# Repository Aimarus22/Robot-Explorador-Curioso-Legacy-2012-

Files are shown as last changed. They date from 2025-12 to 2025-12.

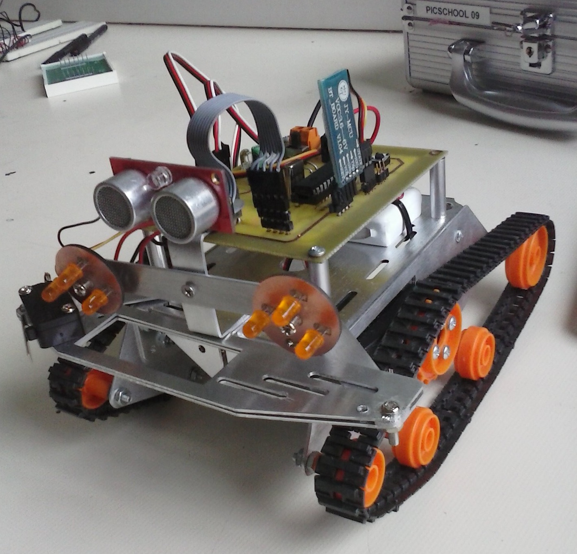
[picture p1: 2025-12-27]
docs/REC.jpg

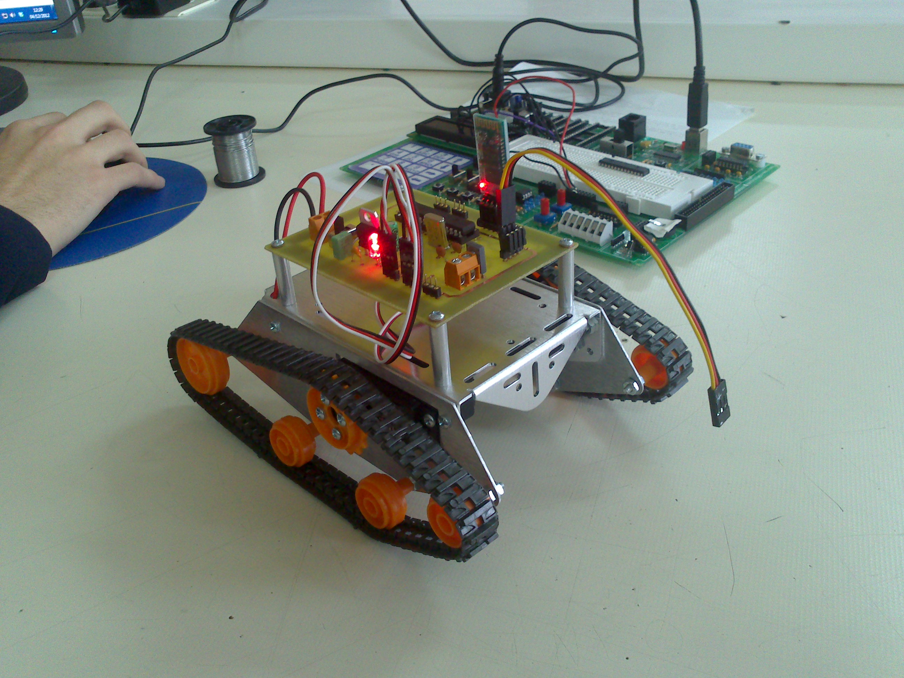
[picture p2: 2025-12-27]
docs/DSC_0086.jpg

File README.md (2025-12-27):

# Robot Explorador Curioso (Legacy 2012) 🤖

> **3er Premio - Premios Don Bosco (DBSariak) 2013**
> *Innovación en Electrónica y Robótica*

Este repositorio sirve como cápsula del tiempo para la preservación digital del proyecto **"Robot Explorador Curioso"**, desarrollado íntegramente en el curso 2012-2013 como proyecto PBL de fin del Ciclo Formativo de Grado Superior en Desarrollo de Productos Electrónicos en **La Salle Berrozpe** (Andoain).

## Objetivos del Repositorio

Este archivo no es solo un backup, tiene un doble propósito académico y de investigación:

1.  **Preservación Histórica:** Mantener accesible el código fuente, esquemas y documentación original tal y como fueron concebidos en 2012-2013, sin refactorizaciones modernas, para documentar el estado del arte de la educación técnica de la época.
2.  **Estudio Comparativo (Arqueología de Software):** Servir como "Línea Base" (v.0) para analizar la evolución de la ingeniería de sistemas embebidos. El objetivo futuro es contrastar estas técnicas "bare-metal" artesanales (control de tiempos por software, gestión manual de registros) con implementaciones modernas (RTOS, periféricos dedicados, TinyML) en la misma plataforma robótica.

## Autores y Créditos
Proyecto desarrollado por el equipo técnico de "Robotic Solutions" (empresa simulada para el proyecto PBL):

* **Axier Albín** - *Desarrollo de aplicación Android.*
* **Jokin Mugika** - *Diseño Mecánico, fabricación de PCB, montaje y puesta a punto.*
* **Aimar Rollán-González** - *Firmware, gerbers y documentación.*

**Institución:** La Salle Berrozpe (Andoain, Gipuzkoa, España).

## Stack Tecnológico (La "Vieja Escuela" de 2012)
El robot destaca por integrar múltiples subsistemas complejos en un microcontrolador de 8 bits con recursos limitados, utilizando técnicas de programación de bajo nivel hoy en desuso en favor de capas de abstracción (HAL).

* **Microcontrolador:** Microchip **PIC16F876A** (8-bit, 20MHz).
* **Lenguaje:** C (Compilador CCS).
* **Hardware:** PCB diseñada a medida en **OrCAD** y fabricada/soldada manualmente.
* **Sensores:** Ultrasonidos SRF08 (protocolo I2C implementado a mano) + Telemetría de batería (Calibración ADC empírica).
* **Actuadores:** Servomotores de rotación continua controlados mediante **PWM por Software (Bit-Banging)**.
* **Comunicación:** Módulo Bluetooth (UART) + App Android nativa (App Inventor).

## Estructura del Repositorio

* `/firmware`: Código fuente original (`main.c`) recuperado del archivo de 2013. Muestra la implementación manual de la máquina de estados y los retardos bloqueantes (`delay_us`) para la generación de señales.
* `/hardware`: Archivos de diseño electrónico (Esquemáticos, PCBs y Gerbers) generados con OrCAD.
* /applet_android : Programa original .apk
* `/docs`: Memoria técnica completa, incluyendo el Plan de Negocio ficticio y diagramas de flujo.

## Nota de Preservación
El código contenido en la carpeta `/firmware` se presenta **"tal cual" (as-is)** fue compilado en enero de 2013. Contiene prácticas de programación específicas de aquel contexto (uso de retardos bloqueantes para temporización, variables globales, números mágicos) que se mantienen deliberadamente para preservar la integridad histórica y permitir el análisis comparativo con versiones futuras optimizadas.

---
*Repositorio mantenido por Aimar Rollán-González como parte del proyecto de investigación sobre evolución de sistemas embebidos (2012-2026).*

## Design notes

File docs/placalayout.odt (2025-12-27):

VISTA GENERAL EN LAYOUT PLUS

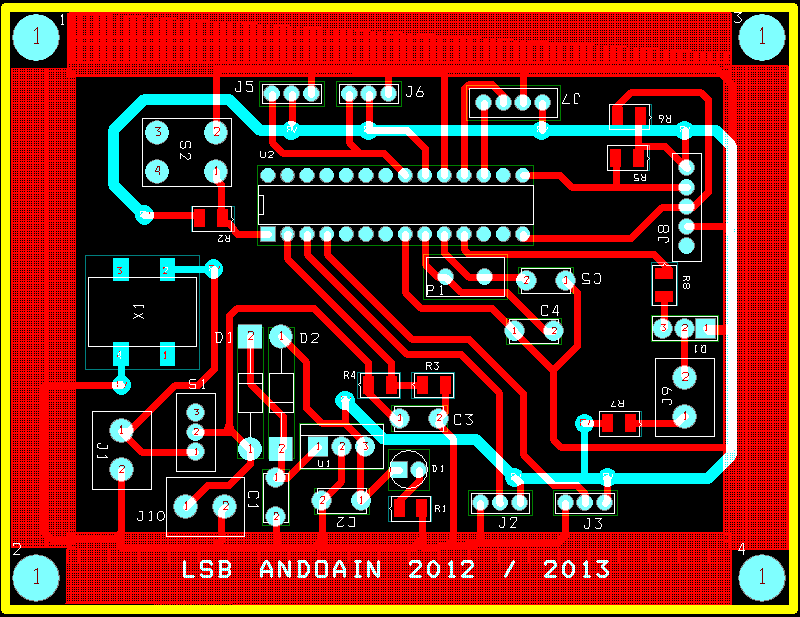
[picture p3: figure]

Instrucciones de montaje:

- Fijarse en la orientación de los componentes.
- El pad cuadrado de algunos componentes corresponde a su pin 1.
- Las resistencias SMD van todas en la cara Bottom.
- Todas las vías son de 1mm.
- Los agujeros de soporte son de 3 mm.
- Broca de 0.8 mm: condensadores, cristal, diodo led, botón reset, regletas y zócalo PIC.
- Broca de 1 mm: diodos, interruptor, LM7805, transistor.
- Broca de 1.2 mm:Regleta naranja (batería, cámara y linterna).

C1: 330nF P1: Cristal

C2: 100nF Q1: Transistor BD139

C3: 1uF (pol.) R1: 220Ω

C4: 22pF R2: 1KΩ

C5: 22 pF R3: 4K7Ω

D1: led verde R4: 4K7Ω

D2: 1N4007 R5: 4K7Ω

D3: 1N4007 R6: 4K7Ω

J1: Regleta batería R7: 15Ω

J2: Regleta motor D R8: 5K4Ω

J3: Regleta motor I S1: Interruptor

J5: Regleta F. C. 1 S2: Pulsador reset

J6: Regleta F. C. 2 U1: LM7805

J7: Regleta bluethoot U2: Zócalo PIC 28 patas

J8: Regleta sonar X1: Cargador de batería SMD

J9: Regleta linterna

J10: Regleta cámara

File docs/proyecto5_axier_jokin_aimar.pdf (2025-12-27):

PROYECTO ROBOT EXPLORADOR

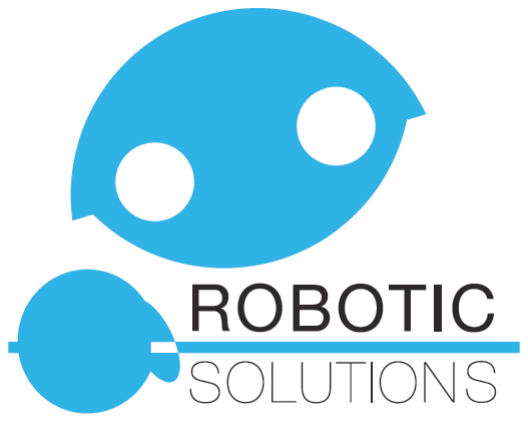
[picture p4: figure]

ÍNDICE

1-. INTRODUCCIÓN | pag. 1
2-. LA IDEA DE NEGOCIO | pag. 2
3-. LOS PROMOTORES | pag. 4
4-. ESTUDIO DE MERCADO | pag. 5
4.1-. ANÁLISIS DEL SECTOR Y LA COMPETENCIA | pag. 6
4.2-. CLIENTES POTENCIALES | pag. 7
4.3-. ANÁLISIS DAFO | pag. 8
5-. EL PLAN DE NEGOCIO | pag. 9
5.1-. EL PLAN DE MARKETING | pag. 9
-. PRODUCTO | pag. 9
-. PRECIO | pag. 11
-. PROMOCIÓN | pag. 12
-. DISTRIBUCIÓN | pag. 15
-. PREVISIÓN DE VENTAS | pag. 15
5.2-. EL PLAN DE INVERSIONES Y COMPRAS | pag. 18
-. INVERSIÓN INICIAL | pag. 18
-.PLANIFICACIÓN DEL PEDIDO | pag. 21
5.3-. EL PLAN DE PRODUCCIÓN | pag. 22
-. UNIDADES A PRODUCIR | pag. 22
-. CÁLCULO DE COSTES Y TIEMPOS | pag. 23
5.4-. EL PLAN DE RECURSOS HUMANOS | pag. 30
-. FORMA JURÍDICA DE LA EMPERSA | pag. 32
5.5-. LOCALIZACIÓN DE LA EMPRESA | pag. 35
5.6-. PLAN ECONÓMICO FINANCIERO | pag. 38
-. PLAN DE FINANCIACIÓN | pag. 38
-. PREVISIONES DE VENTAS | pag. 40
-. BALANCE INICIAL | pag. 41
-. PREVISIÓN DE TESORERÍA | pag. 45
-. CONCLUSIONES SOBRE LA VIABILIDAD | pag. 2

I

6-. MEMORIA TÉCNICA DEL PROYECTO | pag. 47
6.1.- MEMORIA DESCRIPTIVA | pag. 47
6.2.- PLIEGO DE CONDICIONES | pag. 80
6.3.- CÁLCULOS JUSTIFICATIVOS | pag. 83
6.4.- PLANOS Y ESQUEMAS | pag. 90
6.5.- PROGRAMACIÓN DEL PIC | pag. 91
6.6.- CREACIÓN DEL APPLET DE ANDROID | pag. 91
6.7.- CÁLCULO DEL COSTE DEL PROTOTIPO | pag. 94
7-. CONCLUSIÓN | pag. 98
8-. BIBLIOGRAFÍA | pag. 99
ANEXO I: RESULTADOS DE LAS ENCUESTAS DEL ESTUDIO DE MERCADO
ANEXO II: PLANOS DE ORCAD CAPTURE
ANEXO III: PLANOS DE ORCAD LAYOUT
ANEXO IV: PROGRAMA COMPLETO EN LENGUAJE C

ANEXO VI: DATASHEETS DE LOS COMPONENTES DEL CIRCUITO ANEXO VII: MANUAL DE USUARIO

II

## 1-. INTRODUCCIÓN

En el presente informe se expondrán todos los detalles de nuestro proyecto así como la presentación de nuestra empresa ROBOTIC SOLUTIONS. Trataremos de que todo el trabajo de estos últimos meses quede reflejado en él.

## 2-. LA IDEA DE NEGOCIO

Una idea de negocios es una descripción de un posible negocio de éxito. Para que sea buena ha de cumplir ciertos requisitos, tales como:

– | Ha de ser breve, clara y atractiva.
– | Ha de cubrir una demanda no satisfecha en la sociedad, o en caso de que
ya esté cubierta, ofrecer algo mejor o más barato que lo ya existente.
– | Ha de ser rentable económicamente.
– | Su fabricación ha de ser viable para la empresa que la quiera desarrollar.

Nuestra idea de negocio es la de construir un robot explorador de conductos de aire acondicionado y venderlo a buen precio en un nicho de mercado poco explotado, pero también dejando un margen para futuros nuevos productos relacionados con la robótica.

Para desarrollar esta idea y ver si es viable haremos un estudio de mercado, tal como veremos en el apartado 4.

Por otra parte, el nombre de nuestra empresa será: ROBOTIC SOLUTIONS S.coop. (utilizaremos la Cooperativa como forma jurídica de constituir nuestra empresa). Ofreceremos, tal como su nombre indica, soluciones robóticas. Nuestro mercado estará enfocado inicialmente a pequeños robots móviles, destinados a brindar apoyo industrial o doméstico en tareas en las que el ser humano no pueda llegar.

Nuestro logotipo empresarial es el siguiente:

ROBOTIC SOLUTIONS apuesta por la innovación, la creatividad y la calidad de sus productos, así como un precio asequible para llevar sus soluciones robóticas al máximos número de personas.

## 3-. LOS PROMOTORES

Los promotores de este proyecto somos:

– | Axier Albín.
– | Jokin Mujika.
– | Aimar Rollan.

Somos tres técnicos superiores en electrónica, formados en La Salle Berrozpe de Andoain, en la promoción de 2011 – 2013.

## 4-. ESTUDIO DE MERCADO

A través de esta investigación queremos comprobar haber si tenemos un nicho sin explotar en el mercado y en el caso contrario, averiguar si hay un hueco en el mercado para lanzar nuestro producto y saber qué nos diferencia de nuestros posibles competidores en cuanto a las ventajas como a las desventajas.

Para ello necesitaremos saber la aceptación que tendrá nuestro producto en el mercado a que precio estarían dispuestos a comprarlo y por qué comprarían nuestro producto en vez de el de nuestros competidores.

Las fuentes de información serán las siguientes: El mercado objetivo (competencia), posibles clientes, Internet, Instituto nacional de Estadística, Boletín Oficial del Estado (BOE), Registro Mercantil, Registro de la Propiedad, Oficina Española de Patentes y Marcas...

La Técnica de recolección de datos que utilizaremos en gran medida serán las encuestas, ya sean individuales o en grupo, “Focus Grup” y sondeos. Una muestra de nuestra encuesta realizada se adjunta en el Anexo I del presente informe.

4.1.- Análisis del sector y la competencia:

El sector de la robótica en España no está muy masificado, pero las pocas empresas existentes poseen productos adaptados a todas las necesidades de los potenciales clientes. En el País Vasco no existe ninguna empresa que venda robots de inspección de conductos de aire acondicionado, por lo que esa puede ser nuestra principal baza, a pesar de que hoy en día la venta online está en boga y casi todos los competidores tienen una cobertura nacional.

Principales competidores:

– Iberbotics. Santander. Producen y venden el robot explorador de conductos iVision 1.0, un robot de excelente apariencia, robusto, fiable, con 5 años de garantía y una vida útil estimada de unos 15 años.
– Robotnik Automation. Valencia. No poseen robots de inspección de conductos de aire, pero en las categorías de vigilancia, exploración y rescate, sus modelos parecen insuperables. Sus robots son de gran tamaño y de precios astronómicos. Tienen el monopolio de las agencias de protección civil así como las policiales.
– Eventronics. Alicante. Disponen de varios modelos de robots de inspección e incluso limpieza (por medio de escobillas rotativas acoplables e inyección de aire y productos desinfectantes) con bastante buena pinta.
– Trenz-Cleaner. Barcelona. Un único modelo de robot explorador y limpiador de conductos. El robot parece un poco “casero” y su página web no es muy profesional.
– Quark Robotics. Madrid. Su producto estrella es el Cruiserbot, un robot explorador de apariencia muy robusta y compacta, capaz de superar cualquier obstáculo dentro de una tubería.

– Roboserv. Tarragona. Disponen de tres modelos de robot exploradores, con un diseño avanzado y diseñados específicamente para explorar conductos de aire.

Todas estas empresas venden sus robots bajo presupuesto, adaptándolo a las necesidades del cliente, pero ninguno baja de los 3000 euros.

Con estos datos, y teniendo en cuenta que todos venden sus productos a nivel nacional con soporte técnico incluido, nuestra oportunidad de hacernos un hueco en el mercado es ofreciendo un producto considerablemente más barato que el de ellos.

4.2.- Clientes potenciales:

Nuestros clientes potenciales serán principalmente las empresas de instalación, mantenimiento y limpieza de aires acondicionados. En menor medida instituciones gubernamentales y de servicios de seguridad, y algún caso aislado de alguna institución arqueológica. Venderlo como juguete es otra opción, o incluso en centros educativos.

Como uso doméstico no tiene aplicaciones, por lo que nuestra área se reduce al ámbito profesional específico; además cada empresa necesitaría como máximo, y siendo muy optimistas, cinco robots exploradores en caso de empresas grandes con varias inspecciones simultáneas. Además, hay que tener en cuenta que el producto tiene una vida útil bastante larga, de unos cinco años aproximadamente, y que posee un año de garantía; por lo tanto una vez vendido obtendremos poco beneficio del mismo cliente en los primeros años.

En el País Vasco existen una centena de clientes potenciales dedicados al mantenimiento y limpieza de conductos, por lo que es imperativo ampliar el mercado a empresas de seguridad privada, ya que las instituciones gubernamentales, policiales y arqueológicas son tan reducidas en número que una venta sería casi un milagro.

4.3.- Análisis DAFO:

Debilidades:

– | Diseño sencillo.
– | Chasis no demasiado robusto.
– | El producto no es nuevo en el mercado.

Amenazas:

– | Pocos clientes potenciales.
– | Sector muy competitivo.
– | Producto de larga vida (pocas ventas por cliente).

Fortalezas:

– | Precio más bajo que la competencia.
– | Manejo vía smartphone y tablet.

Oportunidades:

– | En el País Vasco no hay empresas que vendan este producto.
– | Podemos venderlo online a otras comunidades o incluso a otros países.

## 5-. EL PLAN DE NEGOCIO

5.1-. PLAN DE MÁRKETING Y VENTAS

Este apartado consiste en establecer una estrategia con el objeto de introducir el producto o servicio en el mercado, alcanzando el volumen de ventas inicialmente previsto. Esta estrategia se funda principalmente en las decisiones sobre el precio, las decisiones de promoción y las decisiones de distribución.

PRODUCTO

Nuestro producto estrella, y único producto de momento, todo hay que decirlo, es el robot explorador “Curioso”, ideado para introducirse por los conductos de ventilación de aires acondicionados y detectar su estado interno. Dónde el ojo humano no ve, el robot
entra en acción, pues
gracias a sus sensores
puede enviar información al usuario. Se dirige desde un dispositivo Android y posee un precio competitivo.

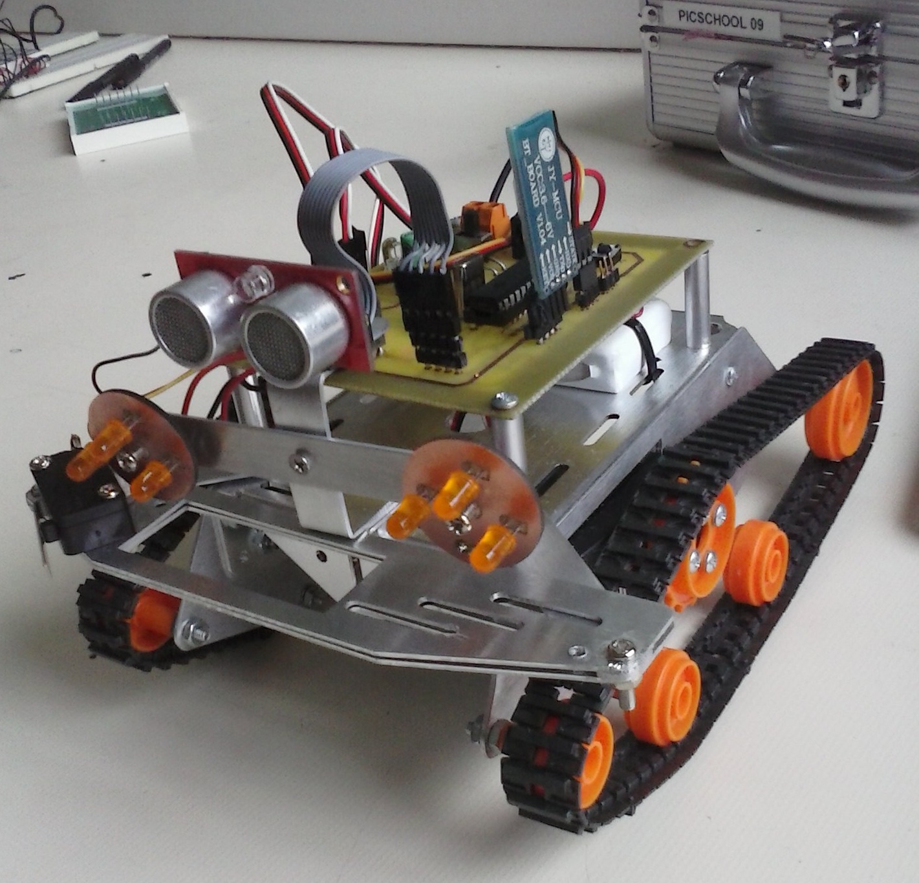
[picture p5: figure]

A pesar de que está
diseñado | para | explorar
conductos de aire y estar
destinado | para | las
empresas de instalación y
limpieza | de | aire

acondicionado, este robot puede ser utilizado para un mayor número de actividades, tales como: vigilancia y reconocimiento en empresas de seguridad y protección civil, en casos de

catástrofes para la búsqueda de personas, inspecciones arqueológicas e incluso como “juguete” en centros educativos... Esto nos abre el mercado y nos posibilita venderlo en varios sectores, aparte del antes citado.

El producto está fuertemente competido por empresas del sector de la robótica, pero casi todos ellos tiene precios astronómicos y su venta está muy especializada a empresas concretas. Nuestra oportunidad es la de ofrecer un producto asequible económicamente, aparte de fiable y fácil de manejar a través de cualquier teléfono móvil.

El robot lo recibirá el cliente una vez pedido en un plazo máximo de 5 días, correctamente embalado en una caja de cartón a medida y con su correspondiente manual de instrucciones.

En el futuro y si todo va bien, introduciremos nuevos productos robóticos para otros ámbitos diferentes al del explorado “Curioso”.

PRECIO

La relación calidad precio que ofrecemos es inmejorable, hecho que convierte nuestro producto en asequible para un gran número de clientes potenciales (pequeñas y medianas empresas, instituciones y particulares). Además, ofrecemos la posibilidad de pago en tres plazos, para así facilitar la adquisición del producto a clientes con limitaciones económicas.

Por otro lado, la elaboración de presupuestos personalizados para cada cliente, hace que sólo paguen por los servicios que quieran recibir. Estamos abiertos a todo tipo de negociaciones y propuestas, ya que nuestro principal objetivo es la captación de nuevos clientes y abrirnos un hueco en el sector.

Los criterios para la imputación de precios estará fijado mediante “márgenes”; esto es el precio de coste unitario (materiales, electricidad, maquinaria, mano de obra...) más un margen de beneficio que queremos obtener. En este caso, el margen de beneficio que queremos rondará por el 10% del coste de producción del robot.

Tal como se detallará en el apartado de producción, el coste de producción del robot es de 336, 38 €.

Aparte de eso, también ofreceremos un servicio técnico y una garantía en caso de reparaciones o mantenimiento, hecho que elevará el precio en 50 € en caso de optar por la garantía de dos años.

Robot explorador “Curioso” con un año de garantía: 650 €

Robot explorador “Curioso” con dos años de garantía: 700 €

La política de precios que vamos a seguir en ROBOTIC SOLUTIONS es la siguiente:

– Los tres primero años mantendremos las tarifas de los productos, pero desarrollando una cantidad elevada de ofertas, con el fin de atraer al mayor número de clientes posibles para que conozcan el nuevo robot; es decir seguiremos una “estrategia de alto valor” (que se aplica a aquellos productos de alta calidad pero que se venden a un precio un poco más barato del que realmente les correspondería en el mercado).

– El precio del robot variará según la demanda: Si una empresa pide más de 5 robots en un pedido, se le aplicará un 10% de descuento; si pide más de 10 un 20% de descuento. Estos descuentos no serán aplicables a la empresa AUTOMAT, ya que es nuestra garantía en los primeros años y la principal interesada en nuestro producto.

– El I.V.A. No está incluido en los precios antes citados.

PROMOCIÓN

Nuestra principal arma de promoción será mediante Internet. Uno de los miembros del equipo posee conocimientos de diseño web y se encargará de crear y mantener una página web de la empresa actualizada con los productos a vender. Utilizará estrategias SEO y de marketing online para promover nuestros productos, así como el renombre de ROBOTIC SOLUTIONS. Se calcula que a partir del sexto mes comenzarán a verse resultados en cuanto al posicionamiento en los principales motores de búsqueda así como un tráfico de visitas considerable. Aparte de esto utilizaremos el emailing para darnos a conocer y enviar ofertas a los clientes potenciales. También pondremos un anuncio mensual utilizando el servicio de Google Adwords para promocionar nuestro producto en Internet.

El gasto que conlleva esto (no incluyendo las horas del técnico, que se incluirán dentro de la nómina general), es la compra del dominio y el alquiler anual de un alojamiento web, más el precio mensual de Google Adwords. Los precios que esto conlleva se muestran a continuación:

– Compra de dominio con el nombre www.roboticsolutions.com, más alojamiento web en la empresa Arsys: 8 € mensuales.

– Servicio de Google Adwords de publicidad: Comenzaremos con una cuota de 50 € mensuales para la modalidad de coste por click (CPC). Esta cuota la iremos aumentando exponencialmente a medida que haya beneficios en la empresa.

– | Gasto total inicial: 58 € mensuales.
– | Gasto anual en promoción: 656 €

Además de esto, crearemos tarjetas de visita personalizadas para cada socio, con el logotipo de la empresa y nuestro puesto. También crearemos catálogos en papel para distribuirlos a nuestros clientes potenciales y que nos sirvan como elemento de marketing.

Las encargaremos a la empresa VISTAPRINT, una de las imprentas más baratas del mercado.

CONCEPTO | PRECIO LOTE | CANTIDAD | TOTAL
250 Tarjetas de visita | 12,95 € | 3 | 38,85 €
250 catálogos | 180,46 € | 1 | 180,46 €
Gastos de envío | 8,95 | 1 | 8,95 €
TOTAL | | | 228,26 €

Mostramos una muestra de nuestro catálogo:

DISTRIBUCIÓN

Nuestro campo principal de actuación es a nivel local, especialmente con la empresa AUTOMAT y clientes potenciales de la zona, pero a medida que nuestra página web cobre fuerza, esperamos que la cobertura sea a nivel nacional o incluso internacional, ya que en nuestra página web habilitaremos un servicio de compra online, enviando tras la compra nuestro producto mediante servicios de mensajería.

A los clientes de la zona o locales, previo acuerdo, les entregaremos los productos personalmente, demostrándoles en el acto su buen funcionamiento y su manejo. Así como la clave para descargar la aplicación Android que les permita dirigir el robot desde uno o varios de sus propios teléfonos. A los clientes que hagan su compra online y no podamos llevarles personalmente el robot, les adjuntaremos con el envío un manual de instrucciones detallado así como las claves de activación de la aplicación Android.

PREVISIÓN DE VENTAS

Gracias a la empresa AUTOMAT, tenemos aseguradas 15 ventas mensuales fijas durante 27 meses. Durante ese plazo, toda nuestra estrategia de marketing debe proporcionarnos los suficientes nuevos clientes potenciales como para hacer sostenible nuestra empresa una vez finalizado nuestro contrato con AUTOMAT. Hemos de conseguir al finalizar los 27 meses, como mínimo, 12 ventas mensuales, para, una vez finalizado nuestro contrato con AUTOMAT, no vernos obligados a cerrar nuestra empresa. El gran reto es pues, que a partir del 4 año la empresa siga siendo rentable.

Durante los 6 primeros meses no esperamos grandes ventas, pero una vez que nuestra página web tenga buen flujo de visitas y seamos conocidos en el sector, esperamos conseguir clientes con la siguiente previsión:

Previsiones de ventas mensuales del primer año:

MES | UNIDADES FIJAS | UNIDADES VARIABLES | TOTAL
Mayo | 15 | 0 | 15
Junio | 15 | 1 | 16
Julio | 15 | 1 | 16
Agosto | 15 | 2 | 17
Septiembre | 15 | 3 | 18
Octubre | 15 | 3 | 18
Noviembre | 15 | 5 | 20
Diciembre | 15 | 7 | 22
Subtotal | 120 | 22
TOTAL | 142

Previsiones de venta en los siguientes 3 años:

AÑO | UNIDADES FIJAS | UNIDADES VARIABLES | TOTAL
Año 2 | 180 | 90 | 270
Año 3 | 120 | 140 | 260
Año 4 | 0 | 180 | 180
TOTAL | 710

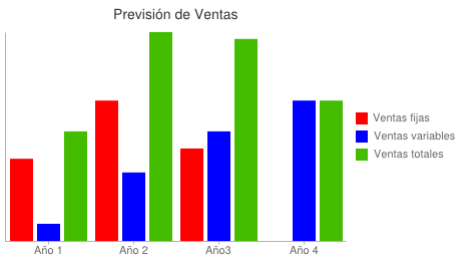
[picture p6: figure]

Esta previsión de ventas se refiere únicamente al robot explorador “Curioso”, pero durante los 3 primeros años, en el tiempo que nos quede libre en nuestra jornada laboral, aparte de desempeñar tareas de marketing y búsqueda y consolidación de clientes, dedicaremos tiempo a I+D para intentar desarrollar nuevos productos robóticos y comercializarlos.

## 5.2- PLAN DE COMPRAS E INVERSIONES

INVERSIÓN

Para la construcción de la empresa hemos aportado un capital inicial de 4.000 € cada socio, dos ordenadores, el coche de un socio mas 3.000€ de ayuda que nos aporta el gobierno vasco. Eso hace un total de 15.000 € y dos ordenadores mas un coche como capital inicial de la empresa. El alquiler del local son 400 € mensuales y ademas necesitaremos el siguiente equipo:

## Material fungible

Resistencia 1K | 500 | Farnell | ERJB2AF102V (http://es.farnell.com/panasonic/erjb2af102v/resistencia-potencia-1206-1-1k/dp/1751076) | 0,20 € | 100,00 €
Resistencia 220Ω | 500 | Farnell | ERJB2AF221V (http://es.farnell.com/panasonic/erjb2af221v/resistencia-potencia-1206-1-220r/dp/1751064) | 0,19 € | 95,00 €
Resistencia 4K7Ω | 500 | Farnell | ERJB2AF472V (http://es.farnell.com/panasonic/erjb2af472v/resistencia-potencia-1206-1-4k7/dp/1751084) | 0,17 € | 85,00 €
Resistencia 15Ω | 500 | Farnell | | 0,18 € | 90,00 €
Resistencia 3K9Ω | 500 | Farnell | ERJB2AF392V (http://es.farnell.com/panasonic/erjb2af392v/resistencia-potencia-1206-1-3k9/dp/1751083) | 0,16 € | 80,00 €
Transistor NPN | 500 | Farnell | STMICROELECTR ONICS BC139 | 0,22 € | 110,00 €
Condensador 1μ F | 500 | Farnell | EKMG101ETC1R0 ME11D (http://es.farnell.com/united-chemi-con/ekmg101etc1r0me11d/capacitor-alum-elec-1uf-100v-20/dp/1499818) | 0,02 € | 10,00 €
Condensador 22pF | 500 | Farnell | MC0805N220J500 A5.08MM (http://es.farnell.com/multicomp/mc0805n220j500a5-08mm/capacitor-ceramic-22pf-50v-c0g/dp/1694230) | 0,02 € | 10,00 €
Condensador 330nF | 500 | Farnell | MC0805B334K500 A5.08MM (http://es.farnell.com/multicomp/mc0805b334k500a5-08mm/capacitor-ceramic-0-33uf-50v-x7r/dp/1694137) | 0,04 € | 20,00 €
Condensador 100nF | 500 | Farnell | MC0805Y104Z500 A5.08 (http://es.farnell.com/multicomp/mc0805104z500a5-08mm/capacitor-ceramic-0-1uf-50v5v-80/dp/1694338) MM (http://es.farnell.com/multicomp/mc0805104z500a5-08mm/capacitor-ceramic-0-1uf-50v5v-80/dp/1694338) | 0,02 € | 10,00 €
Cristal | 500 | Farnell | FOXLF040 (http://es.farnell.com/fox-electronics/foxlf040/cristal-4mhz-20-pf-agujero-pasante/dp/2057944) | 0,37 € | 185,00 €
Regulador | | Farnell | FAIRCHILD SEMICONDUCTO R LM7805CT | 0,28 € | 140,00 €
Interruptor | 500 | Farnell | SSA12G (http://es.farnell.com/te-connectivity-alcoswitch/ssa12g/switch-slide-spdt-20v-through-hole/dp/6410017) | 1,85 € | 925,00 €

Diodo | 500 | Farnell | 1N4007 | 0,14 € | 70,00 €
LED, 5mm, Blanco | 500 | Farnell | OVLEW1CB9 | 0,59 € | 295,00 €
Bluetooth | 15 | Farnell | JY-MCU BT BOARD v1.04 | 8,37 € | 142,29 €
Microcontrolador PIC | 500 | Farnell | PIC16F876A-I/SP (http://es.farnell.com/microchip/pic16f876a-i-sp/ci-mcu-flash-8-bits-16f876-sdil28/dp/9761314) | 3,44 € | 1.720,00 €
Final de carrera | 500 | Farnell | HONEYWELL S&C V15W11-DZ200A02-W2 (http://es.farnell.com/honeywell-s-c/v15w11-dz200a02-w2/interruptor-spdt-5a-palanca-recta/dp/2065396) | 5,75 € | 97,75
Led encendido verde | 500 | Farnell | LUMEX SSL-LX5093GT (http://es.farnell.com/lumex/ssl-lx5093gt/led-5mm-green-50mcd-565nm/dp/7605705) | 0,05 € | 25,00 €
Receptáculo, 2,54 mm, simple, 4 vías | 500 | Farnell | CES-104-01-T-S (http://es.farnell.com/samtec/ces-104-01-t-s/receptaculo-2-54-mm-simple-4-vias/dp/1667510) | 0,36 € | 180,00 €
Conector hembra 12V SMD 2.1mm | 500 | Farnell | FC68148S (http://es.farnell.com/cliff-electronic-components/fc68148s/dc-socket-smd-dc-10as-2-1mm-pin/dp/1889309) | 0,88 € | 440,00 €
Regleta de conexión con tornillo | 500 | Farnell | MC24356 (http://es.farnell.com/multicomp/mc24356/terminal-block-eurostyle-2pos-26/dp/1624287) | 0,15 € | 75,00 €
PIC 28 pines | 500 | Farnell | 2227MC-28-03-05-F1 | 0,82 € | 410,00 €
Jumper 2 hilos 6 pulgadas | 500 | Farnell | | 0,95 € | 470,00 €
Jumper 5 hilos 4 pulgadas | 500 | Farnell | | 0,95 € | 470,00 €
Placa terminada | 500 | 2cisa | | 1,50 € | 750,00 €
Total | | | | | 7.004,75 €

## Mobiliario Local

Mesa de trabajo | 2 | Ebay | | 89,90 € | 179,8
Estación de soldadura | 2 | Ebay | | 64,70 € | 129,4
Mesa recepción | 1 | ikea | EXPEDIT | 131,98 € | 131,98 €
Silla para visitas | 2 | ikea | SNILLE | 16,99 € | 33,98 €
Silla recepción | 1 | ikea | FINGAL | 39,99 € | 39,99 €
Silla trabajo | 2 | ikea | SNILLE | 17,99 € | 35,98 €
Total | | | | 361,55 € | 551,13 €

Gastos administrativos
Trámites | 250,00 €
Alquiler local | 400,00 €
Fianza local | 800,00 €
Gastos de publicidad | 228,26 €
Total | 1.678,26 €

Nuestro primer gasto ha sido constituir la Sociedad Cooperativa; para ello hemos necesitado 3000 € de bote común más 250 € de gastos de constitución. Una vez formada la Cooperativa hemos utilizado esos 3000€ de bote común para la compra de materiales.

Hemos comprado en bloque los componentes pequeños para la construcción de 500 robots, ya que así nos sale más barato que comprarlos cada mes ahorrándonos bastante dinero. Compraremos cada mes los componentes más costosos con un stock de 10 robots, teniendo en cuenta el pedido de AUTOMAT.

Por otra parte hemos comprado el mobiliario para el acondicionamiento del local, buscando los mejores precios en el gran abanico de proveedores que hay, pero sin olvidar la calidad.

Para la selección de los proveedores nos hemos fijado básicamente en el precio y en la disponibilidad que tiene el proveedor para proporcionarnos los materiales para un pedido inesperado ya que las fechas de entrega de los proveedores, en este caso Farnell, no suelen superar la semana.

Con todo esto, la inversión inicial necesaria seria la siguiente, y por lo tanto, no necesitamos pedir ningún préstamo al banco.

Inversión inicial
Mobiliario | 551,13 €
Gastos administrativos | 1.670,26 €
Material fungible | 7.004,75 €
Total | 9.226,14 €

PLANIFICACIÓN DEL PEDIDO

Tenemos un pedido fijo cada mes de 15 robots por parte de AUTOMAT, lo que nos obliga ha hacer un pedido mensual de los componentes mas caros, que serán un mínimo de 15 unidades y siempre manteniendo un stock de 10 unidades por si nuestro departamento de marketing consigue alguna venta. Nuestra filosofía será intentar entregar al momento los pedidos recibidos y siempre mantener ese stock de 10 unidades para poder satis facer cualquier pedido inesperado.

## 5.3.- PLAN DE PRODUCCIÓN

- NUMERO DE UNIDADES A PRODUCIR

Tenemos que producir un mínimo de 15 unidades de robot al mes puesto que ya tenemos con la empresa AUTOMAT un contrato para producir esa cantidad mínima. Aunque después de estudiar el proceso productivo, y calcular cuanto tiempo nos supondría hacer un robot desde cero, que serian 2 horas aproximadamente entre dos trabajadores, podemos fabricar 4 robots por día y en consecuencia 20 unidades de robot en una semana, sabiendo que nuestra jornada laboral consta de 8 horas al día y cinco días a la semana.

Después de comprobar que el mínimo de unidades a producir lo cubrimos en una semana, podríamos fabricar hasta un máximo de 80 unidades en un mes, en los meses que haya 20 días laborables.

- NUMERO DE TRABAJADORES NECESARIO

En el apartado anterior, hemos mencionado que podríamos producir hasta un máximo de 80 unidades por mes, aunque estos cálculos son en el caso que los tres socios de la empresa nos dedicásemos enteramente a la tarea de fabricación del robot.

Nuestra empresa “Robotic Solutions” es una empresa de forma jurídica Cooperativista, formada por tres socios, por lo que no seria viable que los tres socios nos ocupásemos solo de la fabricación, puesto que quedan muchas mas ocupaciones dentro de la empresa que restarían tiempo a la producción.

Como no queremos, ni tampoco seria viable contratar a terceras personas, debemos ocuparnos de muchas cosas; trabajo de oficina (nominas, facturas, pedidos de material, etc.), trabajo de marketing y publicidad, buscar nuevos clientes, tareas de investigación para mejorar el producto e incluso para diseñar nuevos prototipos, reuniones de empresa, reparaciones, etc.

Pero aun teniendo que ocuparnos de las demás tareas a parte de la producción seria suficiente con tres personas trabajando, por lo menos para los tres primeros años en los cuales tendríamos a la empresa AUTOMAT como cliente fijo y seria suficiente con trabajar la mitad de los días del mes produciendo robots y la otra mitad en otras ocupaciones.

CALCULO DE TIEMPOS

El tiempo que necesitamos para la construcción del producto consta de 3 horas y 10 minutos, repartidos de la siguiente manera:

- Montar chasis, ruedas y servomotores → 1h
- Soldar componentes a la placa → 40min
- Cargar el programa de funcionamiento del robot en el microprocesador → 5min
- Colocar finales de carrera, luces y cámara en la carcasa → 30min
- Colocar la placa en el chasis y hacer las respectivas conexiones → 15min
- Colocar la carcasa y finalizar la construcción → 15min
- Pruebas de funcionamiento → 15min
- Empaquetar el robot → 10min

PROCESO PRUDUCTIVO

CÁLCULO DE COSTES Y UMBRAL DE RENTABILIDAD

UMBRAL DE RENTABILIDAD

INVERSIONES EN ACTIVO

Inversiones Años Amortizaciones

Gastos de constitución (Notario) | 250,00 € | 1 | 250,0 €
Alquiler local | 400,00 € | 1 | 400,0 €
Fianza local | 800,00 € | 1 | 800,0 €
Gastos publicidad | 228,26 € | 1 | 228,3 €
Herramientas varias | 200,00 € | 1 | 200,0 €
Estación de soldadura | 129,42 € | 1 | 129,4 €
Mobiliario de oficina | 421,58 € | 1 | 421,6 €
Materiales para stock | 7.004,75 € 1 | 7.004,8 €

Total inversiones 9.434,0 €

COSTOS FIJOS

Costo | Mes Costo anual
ALQUILER | 400 € | 12 | 4.800,0 €
AGUA | 45 € | 12 | 540,0 €
LUZ | 75 € | 12 | 900,0 €
TELEFONO-INTERNET | 49 € | 12 | 588,0 €
SEGURO DEL MOBILIARIO | 1.720 € | 1 | 1.720,0 €
SUELDOS (3 TRABAJADORES) | 1.800 € | 12 | 21.600,0 €
PAGO AUTONOMOS | 450 € | 12 | 5.400,0 €

Total fijos 35.548,0 €

COSTOS VARIABLES

Materia prima para un robot

Componente | Cantidad | Precio unitario (€) Precio total (€)
Resistencia 1KΩ | 1 | 0,20 € | 0,20 €
Resistencia 220Ω | 2 | 0,19 € | 0,38 €
Resistencia 4K7Ω | 4 | 0,17 € | 0,68 €
Resistencia 15Ω | 1 | 0,18 € | 0,18 €
Resistencia 3K9Ω | 1 | 0,16 € | 0,16 €
Transistor NPN | 1 | 0,22 € | 0,22 €
Condensador 1μ F | 1 | 0,02 € | 0,02 €
Condensador 22pF | 2 | 0,02 € | 0,04 €
Condensador 330nF | 1 | 0,04 € | 0,04 €
Condensador 100nF | 1 | 0,02 € | 0,02 €
Cristal | 1 | 0,37 € | 0,37 €
Regulador | 1 | 0,28 € | 0,28 €
2 Motores + chasis | 1 | 45,00 € | 45,00 €
Kit para la oruga | 1 | 25,00 € | 25,00 €
Interruptor | 1 | 1,85 € | 1,85 €
Diodo | 2 | 0,14 € | 0,28 €
LED, 5mm, Blanco | 6 | 0,59 € | 3,54 €
Pulsador | 1 | 0,38 € | 0,38 €
Bluetooth | 1 | 8,37 € | 8,37 €
Microcontrolador PIC | 1 | 3,44 € | 3,44 €
Final de carrera | 2 | 5,75 € | 11,50 €
Sonar ultrasónico | 1 | 33,50 € | 33,50 €

Batería LiPo 7.2V | 1 | 20,00 € | 20,00 €
Cargador de baterías LiPo | 1 | 19,00 € | 19,00 €
Led encendido verde | 1 | 0,05 € | 0,05 €
Receptáculo, 4 vías | 1 | 0,36 € | 0,36 €
Conector hembra SMD | 1 | 0,88 € | 0,88 €
Regleta de conexión | 2 | 0,15 € | 0,30 €
Zócalo-PIC 28 pines | 1 | 0,95 € | 0,95 €
Carcasa del robot | 1 | 28,00 € | 28,00 €
Cámara de video | 1 | 27,00 € | 27,00 €
Caja de cartón | 1 | 3,15 € | 3,15 €
Libreta instrucciones | 1 | 0,85 € | 0,85 €
Placa terminada | 1 | 5,00 € | 5,00 €
Jumper 2 hilos | 2 | 0,95 € | 1,90 €
Jumper 5 hilos | 1 | 0,95 € | 0,95 €
Coste total material | 243,84 €

COSTES FIJOS ANUALES:

Amortización del inmovilizado | 9.434 €
Otros costes fijos | 35.548 €
COSTES FIJOS ANUALES | 44.982 €

COSTO VARIABLE POR UNIDAD PRODUCIDA:

GANANCIAS ANUALES

Coste material unitario = 243,84 €

Unidades = 480 Robot / año

Costos fijos anuales = 44.982,01 € anuales

Coste variable para un Robot = CV_unit. + (C_fijo / Unidades) = 337,55 €

Precio venta robot = 700,00 €

Ganancias = (Precio – costos variables) * Cantidad ventas

Ganancias = 173.975 €

Comprobamos: GANANCIAS = VENTAS - COSTOS VARIABLES - COSTOS FIJOS

Unidades / año | Precio | En total
VENTAS | 480 | 700,00 € | 336.000,00 €
COSTOS VARIABLES | 480 | 243,84 € | -117.043,20 €
COSTOS FIJOS | | | - 44.982,01 €
GANANCIAS | 173.974,79 €

PUNTO MUERTO (Q)

Se conoce como “Punto muerto” al mínimo de unidades a producir para obtener beneficios. Se calcula con la siguiente fórmula:

Q=

Costes Fijos
Precio−Costes variables

Q=

44982
700−248,78

=98,6

Así calculamos que el punto muerto es de 98.6 ventas anuales, o lo que es lo mismo: 8,22 ventas mensuales.

## 5.4-. PLAN DE RECURSOS HUMANOS

Estructura de la empresa

Junta general de socios

Está constituida por la totalidad de socios de la empresa. La junta general es la máxima autoridad en la toma de decisiones, y estas se toman de forma democrática conforme a lo establecido en la Ley de sociedades cooperativas.

La junta se reúne en las siguientes situaciones:

– | Cuando la convoque cualquiera de los socios.
– | Cuando una decisión no corresponda a ningún cargo o no esté claro a
| qué cargo corresponde.
– | Cuando la convoque cualquiera de los cargos directivos de la empresa.
– | Cuando una decisión corresponda a dos cargos, y no haya acuerdo
| entre ellos.

Departamento de producción

Se encarga de la parte interna del proceso de producción, es decir, de elaborar el proyecto y encargarse de que se lleve acabo en la fecha prevista. Su máximo responsable es el jefe de proyectos.

Departamento de administración y finanzas

Se encarga de llevar la contabilidad, de la realización de los presupuestos para los proyectos y de los trámites burocráticos de la empresa. Y su máximo responsable es el jefe de cuentas y personal.

Departamento de marketing

Engloba todas las funciones externas derivadas de la actividad de la empresa: la promoción de la empresa, la captación y el trato con el cliente y los colaboradores y de la interacción con el exterior en general. Su máximo responsable es el gerente de la empresa.

Definición de los puestos

Aimar Rollán será el gerente de la empresa por su mayor experiencia en los negocios y por su mayor capacidad de organización y capacidad de asumir responsabilidades, capacidad de negociación y diplomacia.

Jokin Mugika será el jefe de proyectos por su capacidad de sacar adelante los proyectos, por su capacidad de innovación y organización.

Axier Albín será el jefe de cuentas y personal debido a sus conocimientos de contabilidad y por sus conocimientos sobre recursos humanos y su facilidad para desembolsarse con el papeleo.

Al ser una empresa pequeña no vemos necesario la contratación de ningún otro empleado ya que nos basta para sacar adelante la producción de los robots que nos puedan pedir, puesto que somos capaces de producir 80 robots al mes.

En caso de que la demanda exceda excesivamente la producción nos plantearemos la contratación de algún otro empleado, al igual que si la empresa crece lo suficiente como para necesitarlo., pero en los primeros 3 años no prevemos que suceda tal cosa.

FORMA JURÍDICA DE LA EMPRESA

Robotic Solutions es una Sociedad Cooperativa pequeña. Esta forma jurídica nos permite formar nuestra propia empresa aportando un pequeño capital inicial y ser dueños de ella, siendo los máximos beneficiarios del éxito de la misma. Hemos elegido esta forma jurídica frente a otras por los beneficios fiscales que nos proporciona y por la legislación en cuanto a la toma de decisiones (una persona un boto) y en cuanto al reparto de beneficios según el trabajo aportado.

Las Cooperativas de Trabajo Asociado deberán reunir las siguientes características

- El número mínimo de socios será de tres.
- El Capital Social estará constituido por las aportaciones de los socios.
- El importe total de las aportaciones de cada socio no podrá exceder de un tercio del capital social.
- Los Estatutos fijarán el capital social mínimo con el que puede constituirse y funcionar la Cooperativa, que deberá estar totalmente desembolsado desde su constitución.

TRÁMITES PARA SU CONSTITUCIÓN

La documentación a aportar para la constitución de las Cooperativas de Trabajo Asociado será:

- Certificación negativa del nombre de la Sociedad.
- Escritura Pública.
- Impuesto sobre Transmisiones Patrimoniales y Actos Jurídicos documentados.
- Inscripción en el Registro de Sociedades Cooperativas.

Otros documentos:

- Diligenciado y legalizado de los libros sociales y de contabilidad, en el Registro de Sociedades Cooperativas.

TRÁMITES PARA INICIAR LA ACTIVIDAD

Fiscales:

- Solicitud del Código de Identificación Fiscal (C.I.F.), y alta en el Censo de Etiquetas y Opciones I.V.A.
- Declaración de alta en el Impuesto sobre Actividades Económicas (I.A.E) y en el Impuesto sobre Bienes Inmuebles, cuando proceda.
- Declaración previa al inicio de la actividad. Recogida y presentación de impresos: Delegación de Hacienda correspondiente al domicilio fiscal de la empresa.

Laborales:

- Inscripción de la empresa y afiliación de los socios.
- Comunicar la apertura del Centro de trabajo a la autoridad laboral.
- Adquirir y sellar los libros de matrícula de personal y visitas.

Otros trámites:

- Licencia de apertura.
- Inscripción de patentes, modelos de utilidad, diseños industriales, marcas, rótulos y nombres comerciales en el Registro de la Propiedad Industrial.
- Inscripción, en su caso, de inmuebles aportados a la sociedad, en el Registro de la Propiedad Inmobiliaria.

En nuestro caso hemos elegido trabajar como autónomos dentro de Robotic Solutions Scoop. para no tener que tener un sueldo fijo al mes y cobrar según beneficios, así como para facilitar el arranque de la empresa mientras nuestros beneficios no sean muy elevados; además pagamos menos impuestos siendo autónomos. En cuanto la empresa empiece a arrancar y los beneficios empiecen a aumentar, estamos pensando en dejar de ser autónomos y pasar a ser socios contratados para pagar menos impuestos y asegurarnos una mayor cotización a la seguridad social para nuestros futuros intereses.

TRAMITES PARA DARSE DE ALTA COMO AUTÓNOMO

1- Declaración censal (IVA).
2- Alta en el Impuesto de Actividades Económicas (IAE).
3- Afiliación y alta en el Régimen de Autónomos.

Una vez hagamos los tramites necesarios ya estaremos listos para empezar a trabajar pagando cada uno nuestra retención del IRPF, que en este año 2013 esta situado en un 21% por ciento.

## 5.5-. LOCALIZACION DE LA EMPRESA

Nuestra empresa se ubicará en una zona bastante céntrica, como es el barrio de Gros en San Sebastián. Es un local lo suficientemente grande y barato, ademas no habría que hacer modificaciones puesto que se encuentra en muy buen estado. Dispone de dos plantas; la planta de arriba es mas pequeña donde pondríamos la zona de oficina, y la de abajo la usaríamos como zona de construcción, producción, laboratorio de pruebas, etc.

La localización de la empresa la hemos decidido por el bajo coste que se pide de alquiler, ademas como es céntrico, tiene la gran ventaja que mucha gente que pase por al lado se fije en el escaparate y corra la voz de que existimos. Como no existen empresas que se dedican a este sector cerca es una ventaja a tener en cuenta.

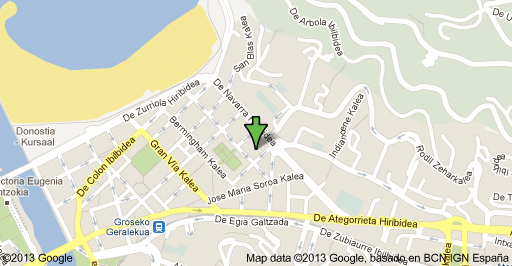
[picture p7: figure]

- Dimensiones del local: 110m²
- Precio: 400€/mes
- Localización: Situado en plaza de Bitoriano Iraola, Gros, Donostia -San Sebastián.
- Descripción del anunciante: Local en Gros, a pie de calle con entrada independiente y muy bien situado. múltiples usos: oficina, academia, estudio, sala de reuniones, trastero, almacén, academia, etc. tiene 105 m2 de planta distribuidos en zona diáfana 80m2 (sin columnas), zona de oficina 20m2, 1 aseo y 20m2 de altillo altillo. ¡Totalmente acondicionado para entrar ya! puede alquilarse por salas, por horas... ¡Máxima flexibilidad! precio negociable en función del uso requerido.

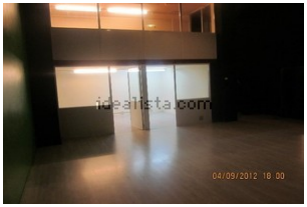
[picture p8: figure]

- Características específicas:
- 110 m² construidos, 104 m² útiles.
- Calefacción independiente eléctrica.
- Agua caliente independiente.
- Distribución y materiales
- Local de 2 plantas.
- Distribución 3-5 estancias.
- 1 aseo.
- Suelos de madera.
- Situado a pie de calle.
- Equipamiento
- Salida de humos y puerta de seguridad

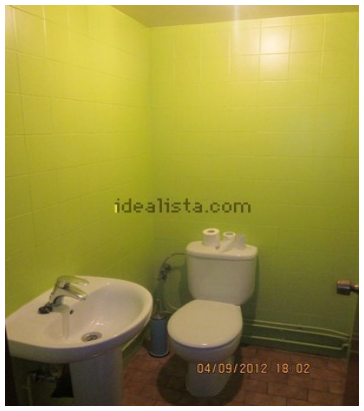
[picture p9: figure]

## 5.6-. PLAN ECONÓMICO-FINANCIERO

En este apartado estudiaremos nuestro plan económico-financiero, viendo como nos financiaremos, nuestro balance inicial, nuestra tesorería y nuestra previsión de resultados para los primeros tres años.

FINANCIACIÓN

Cada socio dispone de 4000 euros iniciales, por lo que disponemos de una financiación propia de 12000 euros. El Gobierno Vasco también nos ofrece una ayuda de 3000 € por crear una Sociedad Cooperativa. Por lo tanto disponemos de una financiación total de 15000 €, y como veremos, no necesitamos solicitar ningún crédito a ningún banco.

De ellos, reservaremos 3000 euros para crear el bote común de la Sociedad Cooperativa que vamos a fundar (ese dinero no lo perderemos, y podremos acceder a él cuando lo necesitemos, aunque nuestra idea es no tocarlo a no ser que sea estrictamente necesario) y los gastos de notario para tal efecto, que se estiman en 250 euros.

Nuestra idea, si es posible, es no necesitar de ninguna financiación externa; es decir, en la medida de lo posible no pedir ningún préstamo a ningún banco; por lo tanto, con los 15.000 € que disponemos hemos de poder crear nuestra empresa y sostenernos hasta que la empresa genere beneficios.

Debido a que la empresa AUTOMAT nos comprará (y pagará) 15 robots mensuales desde el mes de junio, sabemos que a primeros del mes siguiente de la apertura de nuestro negocio tendremos ingresos fijos. Esto nos da mucha seguridad y hace que realmente podamos iniciar nuestra actividad económica sin ayuda externa.

Lo primero que necesitamos saber son nuestros gastos iniciales y anuales:

Gasto inicial y anual:
CONCEPTO | INICIAL | AÑO 1 | AÑO 2 | AÑO 3
Bote común S.coop. | 3.000,00 € | - | - | -
Gastos constitución
(notario) | 250,00 € | - | - | -
Alquiler del local | 400,00 € | 2.800,00 € | 4.800,00 € | 4.800,00 €
Fianza | 800,00 € | - | - | -
Suministros (agua, luz,
gasolina...) | - | 875,00 € | 1.700,00 € | 1.800,00 €
Teléfono e Internet | - | 343,00 € | 588,00 € | 588,00 €
Maquinaria | 500,00 € | - | - | -
Herramientas varias | 200,00 € | - | - | -
Materiales (stock de 20
unidades + 500 placas impresas) | 6.405,60 € | - | - | -
Mobiliario de oficina | 470,00 € | - | - | -
Gastos de publicidad | 228,26 € | 378,00 € | 1.000,00 € | 2.000,00 €
Material de oficina | - | 20,00 € | 40,00 € | 50,00 €
Sueldos 1200€ | 25.200,00 € 43.200,00 € 43.200,00 €
Pago de autónomos | - | 3.850,00 € | 6.600,00 € | 6.600,00 €
Seguro | - | 1.720,00 € | 1.750,00 € | 1.800,00 €
Impuesto de
sociedades 20% | - | 4.322,40 € 12.016,20 € 10.652,00 €
TOTAL | 9.226,14 € 39.508,40 € 71.694,20 € 71.490,00 €
*El IVA no se tiene en cuenta debido a que no está incluido en el precio del robot, y no afecta a esta lista ya que los beneficios obtenidos por el 21% de IVA van íntegros al Estado.

Cada uno de los tres socios aportará a la empresa su ordenador portátil, además utilizaremos siempre software libre, por lo que nos ahorramos el gasto en equipos informáticos y sus licencias. También uno de los socios pondrá a disposición de la empresa su coche particular, para realizar las visitas comerciales pertinentes así como todo desplazamiento necesario, hasta poder comprar un coche de empresa cuando haya los suficientes beneficios.

De este modo, podemos iniciar nuestra actividad empresarial con un capital de 9.226,14 €, teniendo en cuenta que los 3000 € de constitución de la Sociedad Cooperativa siguen estando en nuestro poder. Disponemos de ese capital sin necesidad de financiación ajena.

POLÍTICA DE AMORTIZACIONES

En este apartado se seguirán las indicaciones que la Agencia Estatal de la Administración Tributaria hace al respecto:

Dotación anual a la amortización | % dotación
Gastos de constitución | 20,00%
Gastos de 1er. Establecimiento | 20,00%
Maquinaria | 10,00%
Mobiliario | 10,00%

PREVISIÓN DE VENTAS

Tenemos aseguradas por 27 meses, 15 ventas mensuales a la empresa AUTOMAT, con 2 años de garantía, por lo tanto 700 € por robot, lo que nos da 10500 € mensuales fijos. A esto hay que descontarle los 248,78 € del costo de materiales que cuesta producir cada unidad (sin contar la mano de obra), cada robot nos produce 451,22 € de beneficio. Esto nos proporciona 6768,30 € fijos mensuales de beneficio, durante 27 meses, es decir, hasta agosto del 2015.

Por otro lado, el precio medio de las unidades vendidas a otros clientes es de 677 €, siendo el beneficio de 428,22 € por unidad.

Durante ese plazo, nuestro plan de marketing nos habrá ofrecido, según nuestras previsiones, un mínimo de 12 ventas mensuales, por lo que la previsión a tres años es positiva en todo momento.

INGRESOS | AÑO 1 | AÑO 2 | AÑO 3
Ventas fijas | 47.378,10 € | 81.219,60 € | 54.146,00 €
Ventas previstas | 9.420,84 € | 38.539,80 € | 59.950,80 €
TOTAL | 56.798,94 € | 119.759,40 € | 114.097,20 €

El 4 año, que es el conflictivo, y con una previsión optimista de 15 ventas mensuales, y una pesimista de 10, podemos mantener la empresa abierta hasta conseguir estabilizarnos mediante clientes fieles y una amplia apertura hacia el mercado internacional.

INGRESOS AÑO 4 | OPTIMISTA | PESIMISTA
Ventas previstas | 180 | 120
TOTAL | 77.079,60 € | 51.386,40 €

Teniendo en cuenta que el 4 año tendremos unos gastos fijos de unos 62.000 €, en el caso optimista (que es el que prevee nuestro plan de ventas) sigue habiendo beneficios. En el caso pesimista, tendríamos que reducirnos los sueldos a 900 € mensuales cada socio, o bien tirar de tesorería; pero tendríamos margen de unos cuantos años hasta conseguir las ventas necesarias para que nuestro negocio sea realmente rentable.

BALANCE INICIAL

RESULTADO | AÑO 1 | AÑO 2 | AÑO 3
INGRESOS | 56.798,94 € | 119.759,40 € | 114.097,20 €
GASTOS | 39.508,40 € | 71.694,20 € | 71.490,00 €
BENEFICIOS | 17.290,54 € | 48.065,20 € | 42.607,20 €

Como podemos observar, tenemos un balance positivo para los tres primeros años. Al finalizar cada año ha de haber en nuestra tesorería un balance positivo de un mínimo de 15.000 €. Si hay excedentes, los repartiremos entre los tres socios hasta cubrir el inversión inicial de 4000 € que hicimos cada uno al inicio. Una vez cubierta esta deuda, los beneficios que obtengamos los invertiremos en maquinaría, en un coche de empresa, en I+D, y en planes de marketing para hacer que nuestra empresa crezca aún más. Aunque parezca que hemos obtenido mucho beneficio, recordemos que es a partir del 4 año es cuando empiezan los grandes retos para esta empresa, ya que el contrato con AUTOMAT habrá finalizado y deberemos valernos por nosotros mismos hasta consolidar firmemente nuestra empresa en el mercado con numerosas soluciones robóticas.

PREVISIÓN DE TESORERÍA

| AÑO 1 | AÑO 2 | AÑO 3
Saldo inicial | 6.052,00 € | 23.072,54 € | 38.867,74 €
Beneficios fin año | 17.290,54 € | 48.065,20 € | 42.607,20 €
Subtotal | 23.342,54 € | 71.137,74 € | 81.474,94 €
Retirada de fondos
Amortización | 270,00 € | 12.270,00 € | 270,00 €
Inversiones | - | 20.000,00 € | 10.000,00 €
Tesorería a fin de año | 23.072,54 € | 38.867,74 € | 71.204,94 €

En esta tabla podemos observar un resultado muy positivo y esperanzador si todas nuestras previsiones son correctas. Al finalizar el segundo año, cada socio podrá recuperar su inversión inicial de 4000 €, quedando en la tesorería una cantidad considerable; algo espectacular para una empresa novel (todo esto gracias a nuestro contrato con AUTOMAT); además, podremos disponer de 20000 € para comprar un coche de empresa y nueva maquinaria, así como aumentar nuestros gastos en publicidad y promoción. El tercer año no dedicaremos dinero a la compra de nueva maquinaria, pero sí a publicidad e I+D, pues tenemos que ser previsores y acumular la máxima cantidad posible de dinero en la tesorería, para afrontar el gran reto de los sucesivos años sin AUTOMAT.

OTRAS PREVISIONES DE VENTAS

Ahora vamos a ver 2 hipotéticos casos. Uno en el que nuestras ventas sean malas, y otro en el que sean pésimas. El tercer hipotético caso, en un supuesto de ventas mayores al que nos hemos propuesto, no se contempla, pero será bien recibido en caso de ser cierto.

VENTAS VARIABLES | AÑO 1 | AÑO 2 | AÑO 3 | AÑO 4
MALAS | 10 | 60 | 100 | 120
PÉSIMAS | 5 | 30 | 50 | 80
| AÑO 1 | AÑO 2 | AÑO 3 | AÑO 4
BENEFICIOS
MALAS | 12.800,00 € | 37.500,00 € | 29.500,00 € | -11.720,00 €
PÉSIMAS | 11.800,00 € | 26.909,00 € | 12.501,00 € | -27.849,00 €
TESORERÍA
MALAS | 18.882,00 € | 24.112,00 € | 26.340,00 € | 14.623,00 €
PÉSIMAS | 17.082,00 € | 11.721,00 € | 13.952,00 € | -13.897,00 €

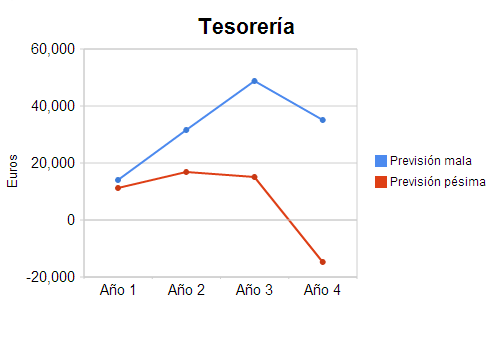
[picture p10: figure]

Como vemos en el anterior gráfico, aun con ventas muy malas, la empresa puede sobrevivir al cuarto e incluso al quinto año como mucho, pero con ventas pésimas la empresa no sobrevive al cuarto año. La empresa AUTOMAT realmente es una garantía y un filón de oro para nosotros, aun con ventas variables malas, pero a partir del cuarto año es imprescindible haber consolidado nuevos clientes y ceñirnos al plan previsto de marketing para poder establecernos.

Existe un tercer escenario hipotético: cerrar la empresa al finalizar el contrato con AUTOMAT y repartirnos la tesorería entre los 3 socios. En ese caso extremo, y previendo pérdidas porque nos ha ido mal, podemos disolver la empresa a los 27 meses y aun así obtener beneficios. Así, por ejemplo, en el caso que tengamos muy malas ventas y poca proyección desde un principio, no haríamos ninguna inversión y al finalizar los 27 meses tendríamos en la tesorería unos 45.000 € a repartir entre tres.

CONCLUSIONES SOBRE LA VIABILIDAD DEL PROYECTO

Tal como podemos observar a través de todos los datos que hemos mostrado, la empresa es viable a corto-medio plazo. Eso sí, siempre y cuando se cumplan nuestras previsiones de ventas.

La empresa AUTOMAT nos sirve para iniciar la actividad y para asegurar unos ingresos fijos considerables durante los primeros dos años y medio, pero la clave del funcionamiento de esta empresa está en nuestras ventas ajenas a AUTOMAT, en la consolidación de clientes nuevos y en nuestra política de marketing. Todo esto es viable si conseguimos los objetivos de venta que nos hemos propuesto, si ello no se logra, la empresa tiene posibilidades de desintegrarse una vez finalizado el contrato con AUTOMAT, a pesar de haber acumulado una tesorería considerable. Por todo ello, es importante dedicar mucho esfuerzo y parte de nuestras ganancias a invertirlas en publicidad y marketing, y confiar en el impacto de nuestra página web para abrirnos camino en el sector.

El objetivo de ventas que nos hemos propuesto es optimista, pero tampoco es demasiado elevado como para no ser realista: se pueden conseguir nuestros objetivos si nos ceñimos al plan de marketing. Por lo tanto, nuestra conclusión es que nuestra empresa sí es viable a corto-medio plazo. Eso sí, y hay que ser precavidos, si nuestro plan de marketing no funciona, una vez finalizado el contrato de 27 meses con AUTOMAT, la empresa pasará por serias dificultades; de ahí la importancia de dedicar parte de nuestros beneficios al departamentos de ventas.

También, como hemos visto, en caso de que no queramos continuar como empresa y ver esta oportunidad como un trabajo temporal para AUTOMAT, cada socio se asegura trabajo por 27 meses con un sueldo de 1200 € netos mensuales y unos beneficios extras al finalizar de 15.000 € cada uno (habiendo recuperado anteriormente la inversión inicial). Con estas conclusiones, iniciar la actividad es más que recomendable aun con esta última proyección; es más, es una oportunidad que no hay que desaprovechar.

## 6-. MEMORIA TÉCNICA DEL PROYECTO

6.1-. MEMORIA DESCRIPTIVA DEL PROYECTO

OBJETO DEL PROYECTO

Nuestro objetivo para este curso era poner en practica los conocimientos aprendidos en el primer curso, para ese fin, estamos elaborando un proyecto. Todos estos conocimientos los estamos aprendiendo mediante la investigación propia y la búsqueda de alternativas para poder conseguir nuestro objetivo final que es la terminación del prototipo.

Como no disponemos de toda la ayuda por parte del profesorado, ya que empleamos el método de estudio PBL, la motivación aumenta pon nuestra parte ya que los logros conseguidos serán por méritos propios y ademas casi con total seguridad no se nos olvidara fácilmente lo aprendido ya que nos resultara mas fácil asimilarlo.

ANTECEDENTES

Tomamos la decisión de sumergirnos en el campo de la robótica, ya que después de realizar los correspondientes estudios, hemos observado que es un sector que esta en pleno apogeo, la implantación de robots en nuestras vidas cotidianas y/o en la industria esta cada vez mas extendida, por lo tanto pensamos que nuestro producto puede ser perfectamente viable, ademas teniendo en cuenta que somos un grupo de jóvenes electrónicos con ganas de aprender y mejorar, podríamos llegar a crear algo realmente bueno y con garantías.

Como bien hemos mencionado, la robótica es un campo que esta en auge, en estos tiempos el uso de la tecnología esta siendo indispensable para el desarrollo.

La robótica tiene y va tener un peso importante, nuestro producto puede encajar perfectamente en el mercado y conseguir de nuestra empresa un perfil nuevo e innovador acorde con los tiempos que corren.

Ademas el precio es muy competitivo, es un factor a tener muy en cuenta para poder conseguir clientes; como tiene un precio asequible nuestros clientes no necesitaran de una inversión demasiado elevada para hacerse con nuestro producto.

MOTIVACIÓN

Al ser un grupo de jóvenes a los que nos gusta la electrónica, nos motiva la idea de poder sacar un producto electrónico al mercado y más aun cuando después de realizar diversos estudios, pensamos que este podría llegar a ser competitivo en el mercado ya que no tenemos mucha competencia en el sector.

Ademas, desde que se nos presentó el proyecto que teníamos que llevar a cabo, nos pusimos manos a la obra con gran ímpetu desde el principio, los tres integrantes del grupo accedimos con gran ilusión al reto.

Nos parece un proyecto realmente interesante así como llamativo, y hemos trabajado duro para finalizarlo con éxito y como nosotros quisimos que fuese desde un principio.

JUSTIFICACIÓN

Realizaremos un robot explorador manejado por control remoto vía bluetooth desde un dispositivo Android (en este caso un teléfono móvil), cuya función principal será acceder a sitios donde los humanos no pueden entrar y dar información del entorne en el que se encuentra. Se mueve gracias a unas orugas que hacen que el robot se pueda agarrar casi a cualquier terreno. Este robot es realmente muy práctico y sencillo de usar, sólo nos hace falta un móvil, una televisión y el mismo robot explorador.

Hemos creado una aplicación Android para el control del mismo, este software es totalmente gratuito. Mediante la aplicación podemos mover el robot en la dirección que más nos apetezca, dar un giro de 180º, saber la distancia que tenemos delante del robot en centímetros, apagar/encender las luces para ver en el caso de que haya mucha oscuridad y también sabríamos si por alguna razón el robot a chocado.

La comunicación con el robot se hará vía bluetooth, para ello disponemos de un modulo Bluetooth JY-MCU V1.04, este modulo se encargará de cambiar la información que enviamos en modo “comunicación serie” al bluetooth y lo mismo a la inversa.

Nuestro robot tiene incorporado un sonar de ultrasonidos para medir distancias, se encuentra en la parte delantera del robot; recogemos directamente la distancia en centímetros, es un sensor SFR08.

También dispone de dos finales de carrera por si se choca, esto hará que se pare de inmediato, garantizando la integridad del aparato.

El robot se impulsa gracias a dos servo-motores de gran fuerza y no muy alto consumo, con los que hará posible hacer frente a cualquier obstáculo.

Tiene una video-cámara con la que podremos ver en todo momento lo que se encuentra delante del robot en tiempo real, para ello solo nos hace falta un televisor.

También tiene leds de alta luminosidad para condiciones de poca visibilidad.

NORMATIVAS Y REGULACIONES

Nuestro producto dispone de un elemento de comunicación radioeléctrica, el dispositivo bluetooth que usaremos para el control del robot. Explicaremos a continuación los estándares y normas que se deben tener en cuenta con este tipo de aparatos para comunicación:

- Bluetooth es una especificación que define redes de área personal inalámbricas (wireless personal área network, WPAN). Se formaliza en el estándar IEEE 802.15.1-2002, desarrolla un estándar basado en la especificación 1.1 de bluetooth. Incluye nivel físico (PHY) y control de acceso al medio (MAC). Se ha publicado una versión actualizada, IEEE 802.15.1-2005.
- 89/336/CEE: Norma Europea CEM. Esta directiva se aplicará a todos los aparatos eléctricos y electrónicos y a los equipos e instalaciones que tengan componentes eléctricos o electrónicos que puedan crear perturbaciones electromagnéticas o cuyo funcionamiento pueda verse afectado por dichas perturbaciones.
- EN 300 328-2: Normativa que regula la compatibilidad electromagnética y el espectro radioeléctrico (ERM). Los sistemas de transmisión de banda ancha; los equipos de transmisión de datos que operen en la banda ISM a 2,4 GHz y que utilizan técnicas de modulación de propagación de espectro radioeléctrico.

- EN 301 489-17: Normativa que regula la compatibilidad electromagnética y el espectro radioeléctrico (ERM), así como la compatibilidad electromagnética (EMC) de equipos y servicios de radio. Apartado 17: Condiciones específicas para los sistemas de transmisión de datos de banda ancha a 2,4 GHz y equipos RLAN de alto rendimiento de 5 GHz.
- EN 60950: Relativa a la seguridad de equipos de tecnologías de la información, entre los que se incluyen los equipos eléctricos empresariales.

Por otra parte, vamos a listar una serie de normas establecidas que se deben tomar en cuenta para crear circuitos impresos y fabricar aparatos electrónicos.

Algunas de estas normas son de obligado cumplimiento en la fabricación de equipos electrónicos:

- UNE 20-050-74 (I). Código para las marcas de resistencias y condensadores. Valores y tolerancias.
- UNE 20-524-75 (I). Técnica circuitos impresos. Parámetros fundamentales. Sistemas de cuadrícula.
- UNE 20-524. Equipos electrónicos y sus componentes. Soldabilidad de circuitos impresos.
- UNE 20-524-77 (II). Técnica de circuitos impresos. Terminología
- UNE 20-531-73. Series de valores nominales para resistencias y condensadores.
- UNE 20-543-85 (I) .Condensadores fijos en equipos electrónicos.
- UNE 20-545-89. Resistencias fijas para equipos electrónicos.

Otras normas a tener en cuenta:

- UNE 20916: 1995: Estructuras mecánicas para equipos electrónicos. Terminología.
- UNE 21302-551: 1996: Vocabulario electro-técnico internacional. Parte 705 propagación de las ondas de radio.
- UNE 21352: 1976: Explicación de las cualidades y funcionamiento de equipos de media electrónicos.
- UNE-EN60933: Sistemas de audio, video y audiovisuales. Interconexiones y valores de adaptación.
- UNE-EN61000-4-3-1998: Compatibilidad electromagnética.
- UNE-EN61030: 1997: Sistemas de audio, video y audio visuales. Bus digital doméstico.
- EN123500: 1992: Especificación intermedia: placas de circuitos impresos flexibles con taladros para la inserción de componentes.

DATOS DE PARTIDA

No encontramos ningún proyecto parecido al nuestro, por lo que todo lo que se ha conseguido ha sido fruto a la investigación.

Hemos dispuesto de diversos manuales y datasheets al igual que de la ayuda de Internet, donde gracias a los numerosos foros de electrónica hemos podido encontrar valiosa información que nos ha ayudado a realizar el trabajo.

ANÁLISIS Y DESCRIPCIÓN

Para realizar este proyecto necesitamos una serie de elementos que separaremos en diferentes bloques:

– | El chasis del robot.
– | Alimentación.
– | Los elementos de propulsión (potencia)
– | Microcontrolador PIC (control).
– | Sensores de detección e iluminación
– | Un sistema de comunicación basado en bluetooth.
– | Una videocámara externa que nos proporcione imágenes.

Después de haber hecho las correspondientes investigaciones y de mirar las distintas características de la amplia gama de componentes que disponemos, consideramos que los ideales o los que mejor se ajustan a nuestro producto son los siguientes. En muchos casos ya disponíamos de algunos componentes en el taller, por lo que nos hemos ajustado un poco también a lo que teníamos ya en mano, mas que nada para evitar más gastos y retrasos.

EL CHASIS DEL ROBOT:

El robot ha de introducirse por los conductos de aire acondicionado, por tal motivo su estructura ha de ser robusta, a ser posible impermeable, y lo suficientemente pequeña para no quedarse atascada y maniobrar bien por los codos y curvas de los tubos. Asimismo deberá poseer una tracción suficiente y una autonomía energética tal que le permita inspeccionar el conducto en su totalidad y regresar a su punto de origen.

Hemos decidido utilizar el chasis del microbot “Home Boe Bot” de la marca MSE
(Microsystems Engineering), en su versión “oruga”, que tiene la siguiente estructura y
dimensiones:
– | 19.5 cm de largo
– | 13.5 cm de ancho
– | 5 cm de alto (solo chasis) | * Versión original del robot: sólo hemos utilizado el chasis.

LA ALIMENTACIÓN:

El robot se alimentará a través de una batería de la clase LiPo de 7,2V, que será la encargada de alimentar todos los componentes electrónicos y mecánicos del robot (motores, microcontrolador, sensores, linterna, etc.). La batería estará controlada por un interruptor que será el encargado de cerrar el circuito para abrir el flujo de corriente, también dispondrá de un conector que permitirá la carga de la batería mediante un adaptador AC, sin necesidad de desmontarla del robot.

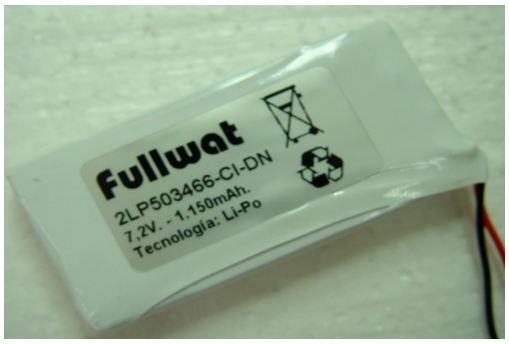
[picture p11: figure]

LOS ELEMENTOS DE PROPULSIÓN (MOTORES):

Para la propulsión del robot hemos aprovechado los dos servomotores de rotación continua de la marca Parallax que venían integrados en el “Boe Bot”, con las siguientes características: Alimentación de +6VDC máx.; Velocidad 60 rpm.; Peso 45.0 gr.; Fuerza 3.4 Kg/cm.; Dimensiones 40.5x20x38 mm.

El microcontrolador PIC será el encargado de controlar los dos motores mediante la modulación por ancho de pulsos (PWM); de esta forma se controla el avance, retroceso y dirección del robot.

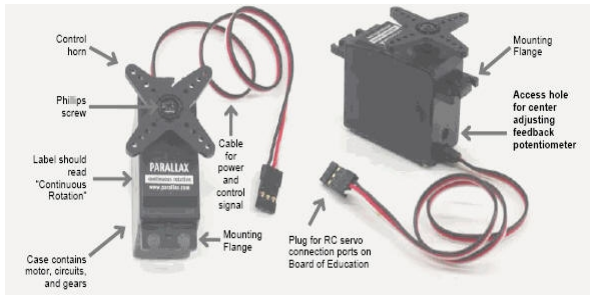
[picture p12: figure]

EL MICROCONTROLADOR PIC:

El microcontrolador PIC es el “cerebro” del robot y de la placa; es el elemento de control que se encarga de que todos los demás elementos estén sincronizados y organizados, sin él el proyecto no sería posible.

Hemos elegido por sus características el PIC 16f876A de la marca Microchip; un micro de 8 bits y 28 patas alimentado con +5Vcc con las siguientes características:

Este micro
tiene las características
suficientes para hacer
funcionar nuestro robot,
debido a que tiene la
capacidad para hacer
una comunicación serie
USART (necesaria para
el bluetooth), y el canal
I2C (pines RC3 y RC4,
necesario para el sonar).

Esquema del patillaje:

LOS SENSORES DE DETECCIÓN E ILUMINACIÓN:

Los sensores de detección son los “órganos de los sentidos” del robot, y serán de dos tipos: de distancia y de choque.

Sensor de distancia:

El sensor que detectará obstáculos y medirá la distancia a la que están, será un sonar de ultrasonidos, concretamente el SFR08 de la marca MSE.

Está compuesto por dos pequeños sonares que aumentan su capacidad de percepción. Es capaz de medir distancias de hasta 6 metros y una distancia mínima de 3 cm.

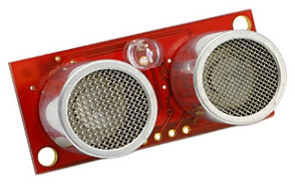
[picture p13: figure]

Especificaciones

Voltaje | 5V
Corriente | 15mA/3mA Standby
Frecuencia | 40 kHz
Mínima distancia | 3cm
Máxima distancia | 6m
Máximo angulo captado | Variable a 1025 en 32 pasos
Tipo de conexión | I2C
Sensor de luz | Sensor frontal de luz
Unidades | Reportado en µS en mm o pulgadas
Peso | 11,3g
Tamaño | 43x20x17mm

Sensores de choque:

Como sensores de choque usaremos dos finales de carrera (bumpers) colocados en la parte delantera del robot, uno en la derecha y otro en la izquierda. Así, en caso de chocar contra un objeto o una pared sabremos por que lado nos hemos chocado.

Iluminación:

El robot poseerá un sistema de iluminación compuesto por 6 diodos LED de alta luminosidad. Estarán colocadas en la parte frontal, 3 a cada lado, a semejanza de los faros de un coche. Estarán controlados de forma manual desde el móvil con la aplicación Android.

EL BLUETOOTH:

Será la parte encargada de recibir y trasmitir todos los datos que recoja el robot, tales como las medidas de los sensores y las ordenes enviados por el usuario. Esta es la parte mas importante del robot, ya que si falla perdemos toda comunicación con él, y por lo tanto todo control sobre él, y seria casi imposible recuperarlo si se encuentra en algún conducto de aire acondicionado. Por este motivo esta parte de la placa tendrá que estar hecha a prueba de fallos.

Para tal fin utilizaremos la tarjeta bluetooth
JY-MCU (http://club.dx.com/forums/forums.dx/threadid.1221753) BT (http://club.dx.com/forums/forums.dx/threadid.1221753)-BOARD (http://club.dx.com/forums/forums.dx/threadid.1221753) v1 (http://club.dx.com/forums/forums.dx/threadid.1221753). (http://club.dx.com/forums/forums.dx/threadid.1221753)04, (http://club.dx.com/forums/forums.dx/threadid.1221753) que trasforma los
datos enviados mediante bluetooth por el

dispositivo Android en formato 232, para que sean comprensibles para el PIC y de este modo podremos controlar en robot y recibir las medidas de los sensores.

Las características de la tarjeta bluetooth JY-MCU BT (http://club.dx.com/forums/forums.dx/threadid.1221753)-BOARD (http://club.dx.com/forums/forums.dx/threadid.1221753) v1 (http://club.dx.com/forums/forums.dx/threadid.1221753). (http://club.dx.com/forums/forums.dx/threadid.1221753)04 (http://club.dx.com/forums/forums.dx/threadid.1221753) son las siguientes:

Especificaciones

Voltaje* | 3,6 y 6v
Corriente | 30mA/10mA Standby
Distancia | 10 m
Led indicador | Si
Peso | 0,2 kg
Tamaño | 15 cm x 15 cm x 5 cm
- A partir de 7V se daña irremediablemente

LA VIDEO CÁMARA:

Utilizaremos una videocámara externa para visualizar imágenes en una pantalla ajena al dispositivo Android de mando. Irá alimentada desde la batería principal del robot.

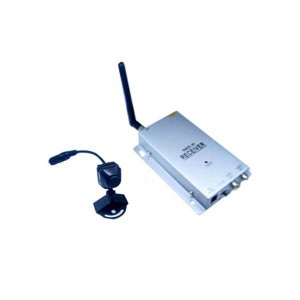
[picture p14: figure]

Características principales

•Agujero de 2,4 GHz tecnología de lentes
•De alta calidad sensor CMOS para obtener imágenes claras •Sistema de múltiples cámaras puede soportar 4 cámaras
•Soporte de adaptación para facilitar la instalación
•Micrófono integrado para
monitorización de audio

DIAGRAMA DE BLOQUES DE LA PLACA

Para realizar este proyecto necesitamos una única placa, y hemos diferenciado cuatro bloques generales: el de alimentación, el de potencia, el de control y el de comunicaciones, aunque este último esté integrado dentro del bloque de control y podamos considerar a nivel práctico tres grandes bloques únicamente.

He aquí el esquema un poco más detallado:

## ALIMENTACIÓN

POTENCIA | CONTROL | COMUNICACIONES

EL BLOQUE DE ALIMENTACIÓN:

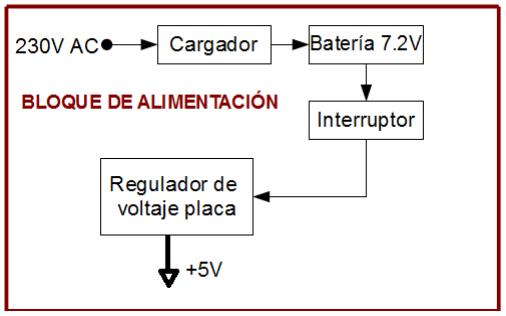
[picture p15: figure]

La alimentación de todos los elementos del robot es suministrada por una batería Lipo de 7.2Vcc, con la posibilidad de recargarla mediante un adaptador AC.

Un interruptor general situado en la placa será el que active o desconecte todo el circuito, seguido de un diodo 1N4007 (que nos servirá para el sensor de batería y como protector de la placa en el improbable caso de que la intensidad supere 1A).

Para suministrar los 5V que necesitan todos los elementos del circuito, implantamos un regulador de tensión LM7805, con dos condensadores no polarizados que le aportan un óptimo funcionamiento. También dispondrá de un diodo de seguridad (D3) que derivará la corriente de retroceso en desconexión.

Para determinar que la batería está suministrando corriente, pondremos en la placa un diodo Led de color verde que nos servirá de indicador visual.

EL BLOQUE DE POTENCIA:

El bloque de potencia está compuesto por dos servomotores, el motor de la rueda derecha y el de la rueda izquierda. Están conectados a +5Vcc y a masa y su tercer pata (out) está ligada a una entrada del PIC (RA1 y RA2), que será el encargado de gobernarlos.

Para que el robot avance el PIC envía una señal en forma de pulsos, que mueve ambos motores hacia adelante; para que retroceda, los dos motores girarán hacia atrás; para que gire a la derecha, el motor derecho avanzara y el izquierdo retrocederá; para que gire a la derecha el motor izquierdo avanzará y el derecho retrocederá; para que haga una curva suave a la derecha, el motor derecho girará a mayor velocidad que el izquierdo; y para que haga una curva suave a la izquierda, el motor izquierdo girará a mayor velocidad que el derecho.

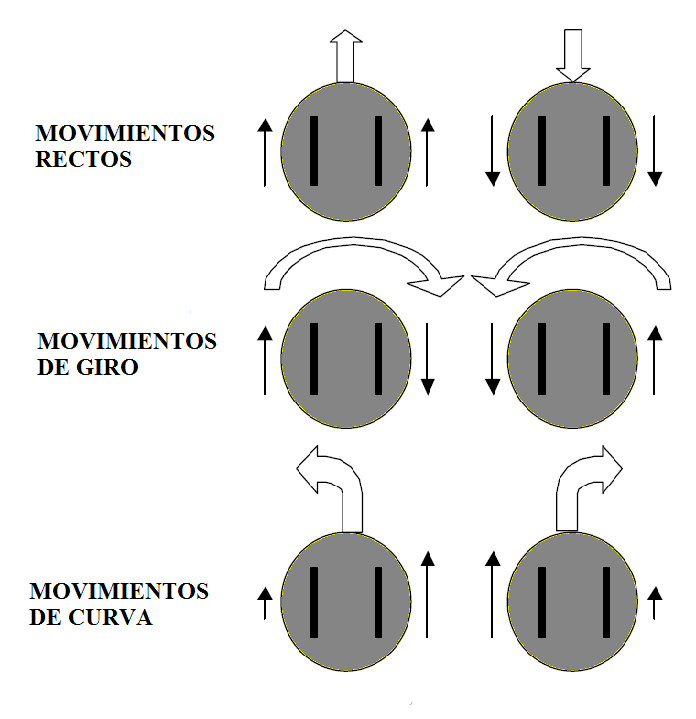
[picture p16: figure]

BLOQUE DE CONTROL:

El PIC está alimentado por +5V y conectado a masa. Para que funcione correctamente hay que ponerle un oscilador (en nuestro caso a 4 Megaherzios) y también le pondremos un reset en forma de pulsador. Al microcontrolador PIC llegan los datos que recogen los sensores y además es el encargado de encender y apagar la linterna si está en modo automático. El Pic recoge los datos mediante sus entradas digitales excepto los datos enviados por el sensor de la batería, que se hará mediante la entrada analógica (RA0). El sonar de ultrasonidos necesita dos entradas específicas, la RC3 y RC4, que están configuradas en este PIC para ser usadas como canal I2C (es un bus de comunicación en serie, que utiliza una entrada para los datos y otra para la señal del reloj).

En este bloque también se encuentra el sensor de la batería, que está alimentado directamente de la batería y conectado a una entrada analógica del PIC (RA0). Este sensor se desarrolla ampliamente en otro apartado del presente documento.

EL SUB BLOQUE DE PERIFÉRICOS:

El bloque de periféricos es un sub bloque del bloque de control, y está compuesto por los sensores de detección (de distancia y de choque), por la linterna y también incluye el de comunicaciones, aunque lo desarrollaremos aparte..

El sonar de ultrasonidos:

Se alimenta a +5V y a masa y sus dos patas que van al PIC han de tener resistencias pull-up de 4K7Ω. SDA se conecta con la entrada SDA del PIC, que corresponde a la pata RC4, y el SCL corresponde a la pata RC3.

Los sensores de choque:

Utilizamos dos finales de carrera a modo de bumpers (parachoques), conectados los dos a la entrada RB0 del PIC, que es la única que se activa por “interrupción externa”. Cuando el robot choque con algún obstáculo, el final de carrera se activará y enviará un “1” al PIC, de esta forma sabremos que el robot ha chocado.

La linterna:

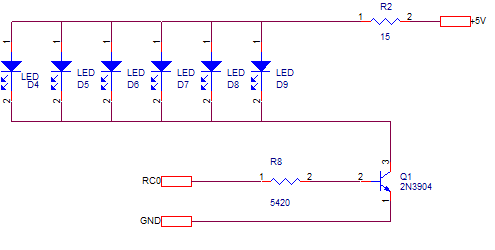
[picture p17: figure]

La linterna está compuesta por 6 leds emisores de luz de alta intensidad cuyos cátodos conectados están conectados directamente a masa y sus ánodos a la fuente de alimentación y a una entrada del PIC (RC0) con una resistencia (de 15Ω -250mW) y un transistor BD139 en modo conmutación, para hacer de interruptor controlado por el PIC; de este modo podemos controlar el apagado y encendido de la linterna vía Android.

BLOQUE DE COMUNICACIONES:

El módulo bluetooth posee cuatro patas, dos para la alimentación y dos para enviar y recibir datos al PIC mediante el USART del micro (pines RC6 y RC7). El USART, "Universal Synchronous / Asynchronous Receiver-Transmitter", controla el puerto serie del micro (TXD y RXD) . Los pines entre el PIC y el módulo bluetooth se cruzan debido a que cuando uno transmite el otro recibe.

SIMULACIÓN DEL PROYECTO

Para nuestro proyecto del robot, hemos tenido que simular algunos de los dispositivos que usaremos en nuestro proyecto. Algunos de dichos dispositivos los hemos simulado en Proteus y también físicamente. En los dispositivos que hemos simulado hasta ahora, se encuentran los siguientes: la parte de alimentación del robot (batería y regulador), el circuito que usaremos para medir el nivel de la batería, el sonar ultrasónico medidor de distancias y los servomotores de rotación continua. También hemos llevado a cabo alguna que otra pequeña prueba con el dispositivo Bluetooth.

Lo primero que simulamos fue la parte de alimentación en Proteus; pusimos la batería y el regulador, con esto conseguimos encender un diodo led y con un voltímetro comprobar que el LM7805 da 5V en su salida. Después de esto incluimos el PIC16F876A y los servomotores y añadimos el sonar SFR08 a la librería del simulador Proteus:

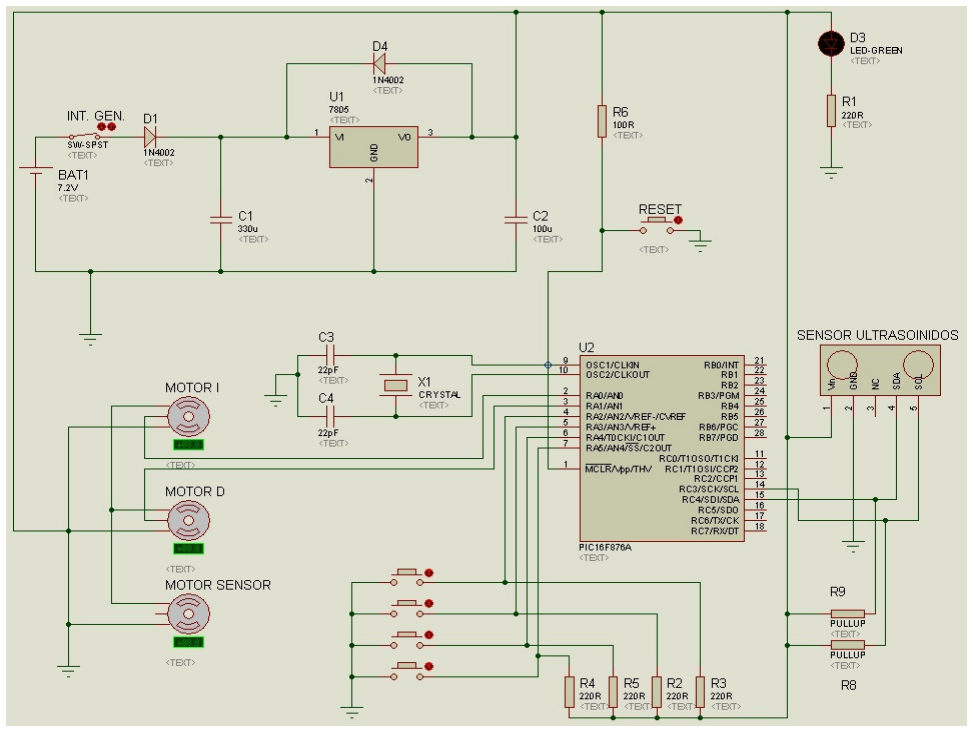
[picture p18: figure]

SERVOMOTORES:

Para probar los servomotores, tuvimos que crear un pequeño programa en lenguaje C puesto que los servos funcionan por PWM, es decir por ancho de pulsos. Una vez montamos el chasis de nuestro robot explorador y los dos servomotores que lo impulsan, también lo probamos físicamente, y usando cuatro pulsadores fuimos capaces de mover el robot hacia delante, hacia atrás y a la derecha e izquierda.

Lo primero que tuvimos que hacer fue regular los servos, sabiendo que cada 20ms se debe de dar un pulso y que dependiendo del ancho del pulso el motor se parará y/o girará a un lado u otro.

En la hoja de datos del producto se cita que para que el motor este parado, deberemos aplicar pulsos de 1,5ms cada 20ms.

Esto fue lo primero que hicimos, aplicamos estos pulsos y pudimos ver que los servos giraban un poco, con la ayuda de una pequeño destornillador giramos un poco un potenciómetro que tiene el mismo servo incorporado, y lo regulamos hasta que se parase de girar.

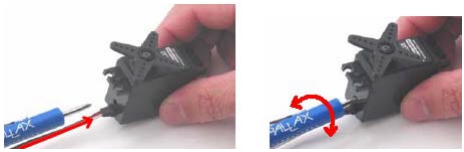
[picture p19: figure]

Una vez regulados los dos servos que conforman la parte de tracción del robot, debíamos de hacer girar los motores en sentido horario y/o anti-horario, por la sencilla razón que los motores están inversos uno respecto al otro, cuando queremos que el robot se mueva hacia delante el servo de la izquierda deberá girar en sentido anti-horario y el servo de la derecha deberá girar en sentido horario. Pero en caso de que queramos que el robot se mueva hacia atrás, tendremos que hacer lo mismo pero a la inversa; para ello se deben de aplicar anchos de pulsos diferentes:

- Para girarlo en sentido horario, se tienen que aplicar anchos de pulsos cada 20 ms, los anchos de los pulsos deben de estar comprendidos entre 1,5 ms y 1,3 ms, siendo los pulsos de 1,3 ms los que harán girar el motor en este sentido a la máxima velocidad posible para estos motores, exactamente 50 rpm es la velocidad mas elevada a la que podrán girar nuestros servos.

- Si en cambio queremos girar los servos en la dirección opuesta, es decir, en sentido anti-horario, el ancho de pulsos que tendremos que aplicar cada 20ms variara entre 1,5ms y 1,7ms. Como en el caso anterior girara a velocidad máxima cuando el ancho de pulsos se mantenga en 1,7ms.

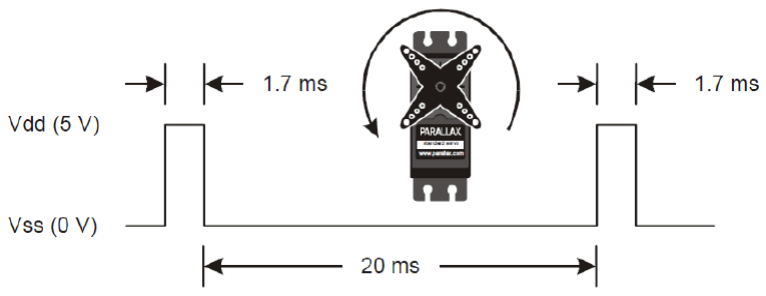
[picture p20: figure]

Después de asimilar esto, pudimos llegar a la conclusión de que no seria difícil poder controlar cuánto tiempo queremos hacer girar el motor, y a la velocidad que queremos que gire, ya que tenemos un rango de 2000 us para variar la velocidad del motor en ambos sentidos, desde 0 rpm hasta 50 rpm cambiando el ancho de los pulsos.

Después hicimos la prueba física no solo para saber como funciona, si no también para comprobar que los servos funcionarían a 5 V, ya que en el datasheet del fabricante se detalla que estos servos funcionan a 6 V. Podemos decir que esta fue la razón que nos condujo a probar los motores y aprender como funcionan.

Lo primero que
hicimos fue, conectar el
servo al PIC como se
muestra el la imagen.
Utilizamos los pines I/O
RA0 y RA1:

Más tarde fuimos elaborado el programa; primero solo movíamos un motor y después los dos hasta que pudimos mover el robot en varios sentidos y direcciones, sirviéndonos de cuatro pulsadores.

SONAR SFR08:

El sonar SFR08 porque funciona mediante el protocolo I2C de comunicación bus en serie. No conocíamos este tipo de comunicación y ademas teníamos que comprobar que el PIC16F876A que habíamos elegido podía comunicarse con el sonar, ya que sólo dispone de este modo para poder
comunicarnos con el.

Un poco de historia sobre I2C sacada de Wikipedia: I²C es un bus de comunicaciones en serie. Su nombre viene de Inter-Integrated Circuit, su diseñador es Philips. (http://es.wikipedia.org/wiki/Philips) La velocidad de transmisión es de 100 Kbps en el modo estándar, aunque también permite velocidades de 3.4 Mbit/s. Es un bus muy usado en la industria, principalmente para comunicar microntroladores y sus periféricos en sistemas integrados (Embedded Systems) y generalizando más para comunicar circuitos integrados entre sí que normalmente residen en un mismo circuito impreso.

La principal característica de I²C es que utiliza dos líneas para transmitir la información: una para los datos y otra para la señal de reloj. También es necesaria una tercera línea, pero esta sólo es la referencia (masa). Como suelen comunicarse circuitos en una misma placa que comparten una misma masa esta tercera línea no suele ser necesaria.

Las líneas se llaman:

- SDA (System Data) por la cual viajan los datos entre los dispositivos.
- SCL (System Clock) por la cual transitan los pulsos de reloj que sincronizan el sistema.

- GND (Masa) Interconectada entre todos los dispositivos "enganchados" al bus.

Las dos primeras líneas son “drenador abierto”, se deben poner en estado alto (conectar a la alimentación por medio de resistores Pull-Up) para construir una estructura de bus tal que se permita conectar en paralelo múltiples entradas y salidas.

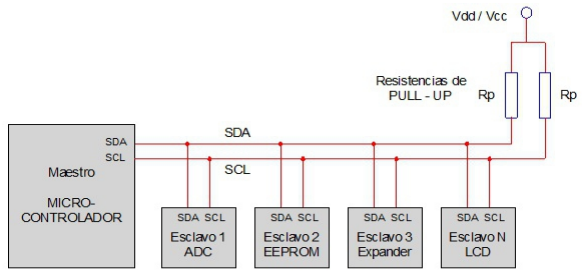
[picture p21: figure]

Bien, una vez entendido un poco como funciona este bus de comunicación serie conectamos nuestro sonar de ultrasonidos a nuestro PIC usando PIC-SCHOOL. Sabiendo que el SFR08 se alimenta a 5V y que necesita dos hilos para la comunicación (SCL y SDL), lo conectamos de la siguiente manera sin olvidarnos claro esta de las resistencias Pull-Up:

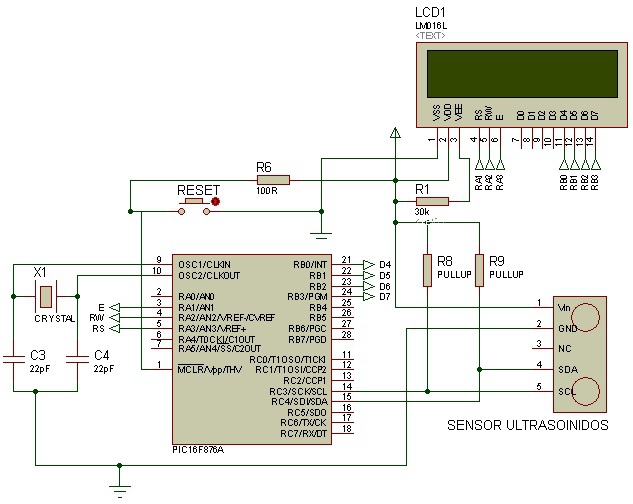
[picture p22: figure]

Como podemos ver en el circuito también hemos usado una pantalla LDC para poder visualizar el valor que esta leyendo el sonar a cada momento. Además el esquema también se compone del circuito de reset del microcontrolador y del circuito del oscilador. El valor estándar de las resistencias Pull-Up es de 4K7 ohm, una vez montamos el circuito cargamos en el microcontrolador un programa que encontramos en Internet para este sonar.

A decir verdad cuando probamos el SFR08 tuvimos algunos problemas para leer los valores, había que hacer algunos cambios en el programa y esto llevo su tiempo. Al final después de varias modificaciones en el programa conseguimos visualizar los valores y con muy buenos resultados de medición por parte del sonar. En cuanto a la resistencias Pull-Up obtuvimos resultados equivalentes con y sin las resistencias. Esto puede deberse que nuestra linea de bus solo se compone de un solo esclavo y en una linea I2C se pueden comunicar muchos dispositivos conectados en paralelo a la linea. Aunque después de leer información en la red sobre estas resistencias, todos o casi todos recomendaban ponerlas en el bus, por lo que nosotros también las añadiremos a nuestro diseño del circuito.

MODULO BLUETOOTH:
El modulo Bluetooth JY-MCU BT_BOARD V1.04 que usaremos para comunicarnos mediante nuestro móvil Android al robot, es otro dispositivo a tener en cuenta en nuestro proyecto.

Este dispositivo, funciona entre 3.3 V y 6 V, consume 30 mA (ideal para nuestro circuito). Su función principal es cambiar la información que

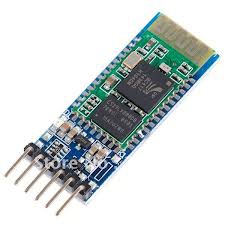
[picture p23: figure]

enviamos y recibimos en USART mediante el puerto serie de nuestro PIC; el modulo Bluetooth recibirá mediante ondas la información y lo cambiara a tipo USART, y por el contrario cuando enviamos información desde el PIC vía serie lo cambiará a Bluetooth.

Una de las primeras dudas que tuvimos fue si había que cruzar los cables RX-TX del microcontrolador con los del dispositivo, en un principio no disponíamos de casi nada de información sobre este tema y estuvimos debatiendo sobre el tema. Quisimos probarlo pero nos surgió otro problema: que necesitábamos un dispositivo exterior que tuviese Bluetooth, el cual seria el encargado de enviar algún tipo de dato mediante ondas. Pero no sabíamos como hacer una aplicación o qué aplicación podíamos usar para este fin. Después de navegar un poco la red y leer en foros, nos quedo claro que sí hay que cruzar los cables TX-RX. Mucha gente había usado este modulo pero conectado a una placa Arduino UNO, en este caso había que cruzarlo por lo que también hay que hacerlo con el PIC. Como había muchos proyectos con Arduino y disponíamos de una de estas placas en clase nos decidimos a probar el modulo con Arduino.

El esquema seria así:

Quedaría así la conexión entre nuestro 16F876A y el modulo Bluetooth:

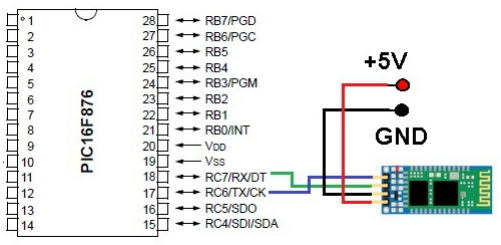
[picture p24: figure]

SENSOROR DE NIVEL DE BATERIA:

Nuestro robot se alimenta a base de baterías, puede que tenga que estar largo tiempo dentro de una tubería y por esa razón hemos pensado en tener la necesidad de saber el nivel de la batería en cada momento.

Después de indagar un poco en la red al final nos convenció un sistema para saber el nivel de la batería bastante sencillo y asequible para nosotros, puesto que se basa en un puerto Analógico Digital del microprocesador. Partimos de que la batería cuando esta cargada al máximo, su valor de tensión sera superior a 7.2 V, esta tensión corresponde a la batería Li-Po que usaremos para nuestro proyecto.

Partiendo de este fenómeno, podremos deducir el nivel de la batería usando el puerto A/D en el Pin AN0. Hemos simulado el circuito que hay que hacer en Proteus para saber si realmente funciona:

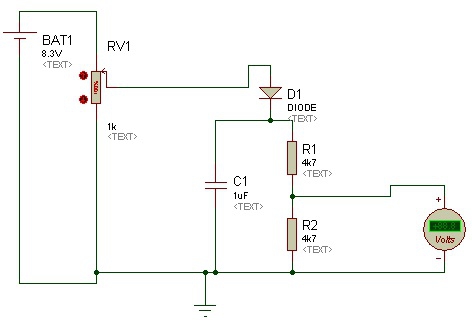
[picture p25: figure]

En este caso hemos puesto una batería con mayor tensión pero básicamente su función es la misma, como en el simulador no varia la tensión de salida usamos un potenciómetro para poder variar la tensión de la batería. Cuando variamos el valor, podemos observar como en el voltímetro recoge valore diferentes, en el caso real esto iría conectado a la entrada A/D del PIC.

La razón de hacer este circuito es porque en la entrada A/D del micro no puede haber tensiones mayores a 5 V. Este divisor de tensión, tal como su nombre indica, divide en dos la tensión real de la batería con lo que conseguiremos que cuando el valor de la batería sea 8V, nosotros en el PIC leeremos 4V.

En el apartado 6.3 de “Cálculos justificativos” se desarrollá más este apartado.

6.2.- PLIEGO DE CONDICIONES

En el presente pliego de condiciones expondremos el proyecto, las normas bajo las que se rige el proyecto y las condiciones generales que se han de cumplir para la fabricación y uso del robot explorador.

OBJETO

El objeto del proyecto es la construcción de un robot explorador con comunicación bluetooth. Dispondrá de un sonar para medir las distancias, un sensor de choque que nos informará si nos hemos chocado, una cámara para ver por dónde se está moviendo y unas luces para alumbrar el camino y posibilitar la grabación el zonas oscuras o sin ningún tipo de luz.

El control de este dispositivo estará realizado a través de un teléfono móvil o tablet con un sistema operativo Android, siempre que este disponga de bluetooth. Esta tarea se realizará a través de una aplicación Android (applet) diseñada por nosotros que habrá que instalar en el dispositivo Android; una vez instalada ya estará lista para usarse.

CAMPO DE APLICACIÓN

El robot explorador en un principio ha sido diseñado para la exploración y revisión de conductos de aire acondicionado en busca de roturas, atascos… Pero también puede ser utilizado para otras aplicaciones tales como exploración y vigilancia, arqueología, uso particular…

No se deberá usar bajo la lluvia ni en lugares de extrema humedad o encharcados. Tampoco se recomienda su uso en pendientes pronunciadas ni en en grandes alturas o sitios con riesgo de caída.

DISPOSICIONES GENERALES

El producto deberá cumplir las normativas y reglamentos referidos al diseño de productos electrónicos explicado en el apartado de normativas y regulaciones.

En cuanto a la seguridad en el puesto de trabajo deberemos cumplir las siguientes normativas.

- Real Decreto 614/2001 de 8.6. (M. Presid., BOE 21.6.2001). Disposiciones mínimas para la protección de la salud y seguridad de los trabajadores frente al riesgo eléctrico.
- Real Decreto 1580/2006, de 22.12 (M. Ind. y Energía., BOE 17.1.2007). Regula la compatibilidad electromagnética de los equipos eléctricos y electrónicos.
- Orden de 9.3.1971 (M. Trab., BBOOE 16 y 17.3., rect. 6.4.1971). Ordenanza general de seguridad e higiene en el trabajo
- Real Decreto 485/1997 de 14.4. (M. Trab. y As. Soc., BOE 23.4.1997). Disposiciones mínimas en materia de señalización de seguridad y salud en el trabajo.
- Real Decreto 486/1997 de 14.4. (M. Trab. y As. Soc., BOE 23.4.1997). Disposiciones mínimas de seguridad y salud en los lugares de trabajo
- Ley 39/1999 de 5.11. (Jef. Est. BBOOE 6.11., rect. 12.11.1999). Promoción de la conciliación familiar y laboral de las personas trabajadoras

ORGANIZACIÓN DEL TRABAJO

El tiempo que necesitamos para la construcción del producto consta de 3 horas y 10 minutos, repartidos de la siguiente manera:

- Montar chasis, ruedas y servomotores → 1h
- Soldar componentes a la placa → 40min
- Cargar el programa de funcionamiento del robot en el PIC → 5min
- Colocar finales de carrera, luces y cámara en la carcasa → 30min
- Colocar la placa en el chasis y hacer las respectivas conexiones → 15min
- Colocar la carcasa y finalizar la construcción → 15min
- Pruebas de funcionamiento → 15min
- Empaquetar el robot → 10min

A la hora de el reparto de trabajos, al ser una empresa pequeña todos tomaremos parte en todas las partes de la producción, nos reuniremos al comienzo de la semana para ver como se nos avecina la semana y haremos el reparto de tareas. Por otra parte Aimar, ya que tiene gran experiencia en el ámbito de las ventas, tomara un par de horas al día para salir con el coche de empresa en busca de nuevos clientes.

Los materiales se almacenarán en las mismas mesas de trabajo, ya que estas disponen de cajones y de cajas en la parte inferior, con todo esto nos evitamos tener que comprar armarios para el almacenaje del material fungible. Por otra parte, los robots ya terminados se apilaran en sus correspondientes cajas en el almacén del que dispone el local.

Los pagos a los proveedores se realizaran a través de trasferencia bancaria, ya que todos nos ofrecen esta posibilidad y es la más cómoda para luego poder realizar todo el seguimiento de los pagos y de las cuentas y tener mas controlada la tesorería.

6.3-. CÁLCULOS JUSTIFICATIVOS

CALCULOS DE LOS ELEMENTOS DE ALIMENTACION:

Como disponemos de una batería como fuente de energía, no necesitamos de muchos cálculos ni elementos para proporcionar electricidad a nuestro circuito. Una vez elegidos los componentes que constituyen nuestro robot; resulta que casi todos si no todos los elementos que necesitamos funcionan o pueden funcionar a 5VDC. Por ejemplo los servomotores necesitan 6VDC para su funcionamiento ideal pero después de probarlos pudimos ver que funcionaban perfectamente, aunque necesitaran mas consumo de corriente. Los demás componentes se alimentan a 5VDC de acuerdo con sus hojas de datos.

Una vez sabíamos la tensión que necesitábamos para el robot y la batería de la que disponíamos(7,2V); nos decidimos a usar un regulador de tensión que nos proporciona 5VDC en la salida, concretamente el LM7805. Al usar este componente el fabricante nos indica que se debe usar dos condensadores en paralelo uno en la patilla de entrada y la otra en la salida; 0,33μF (http://en.wiktionary.org/wiki/%C2%B5A) y 0,1μF (http://en.wiktionary.org/wiki/%C2%B5A) respectivamente para que la señal sea mas limpia y sin ruido. Y la tensión de entrada debe estar comprendida entre 5V y 18V. En el apartado de planos mostramos como esta conexionado dicha sección.

CALCULOS DEL CIRCUITO:

Sensor de nivel de la batería:

A continuación explicaremos cómo realizar un sencillo sensor de nivel de batería con un microcontrolador PIC y un divisor de tensión formado por un condensador y dos resistencias.

La idea es usar una entrada analógica del PIC y convertir ese valor analógico en digital para saber en todo momento el nivel de carga de una batería. Nosotros hemos utilizado una Li-Po de 7.2V, pero este circuito sirve para cualquier tipo de batería.

Lo primero que hay que hacer es medir la tensión de la batería en carga máxima y descargada. En nuestra batería hemos obtenido un valor máximo de 8.45V y uno mínimo de 6.5V. Observamos que la diferencia entre carga máxima y descarga es de 1.95V.

Después crearemos un circuito con un LCD para visualizar el nivel digital de dicha tensión. El circuito será lo más simple posible, como se muestra a continuación, teniendo en cuenta que el PIC necesita una alimentación de 5V.

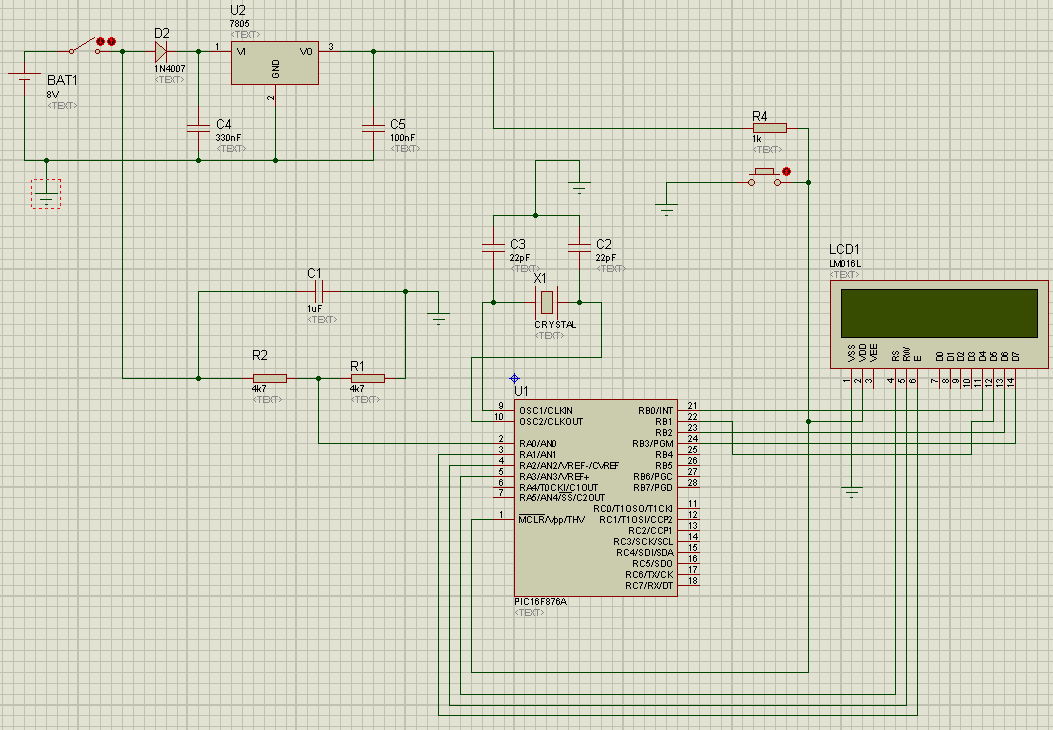
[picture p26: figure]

Antes de realizar el circuito tenemos que saber el valor de las resistencias que usaremos en el divisor de tensión, determinado por la batería elegida (7,2V – 1000mA/h). Para ello debemos hacer un pequeño circuito que ira conectado de la batería a la patilla AN0 de nuestro PIC. Para medir el nivel de la batería hemos colocado un un divisor resistivo, puesto que el conversor ADC del PIC tiene un rango de 0 a 5V, y la batería sera en cualquier caso de 7V o más.

Viendo el pequeño esquema de nuestra derecha, la
relación del voltaje a medir (AN0) con la batería es la siguiente:

V AN0=

V BATERIA−V D1 ⋅R19

R18R19

=0,321⋅V BATERIA−0,7

Sabiendo | esta | formula, | podremos | calcular
teóricamente el valor de las resistencias.

Procederemos a calcular el valor de las resistencias del divisor de tensión sabiendo:

- V AN0 = 4V entrarán como máximo por el ADC
- V D1 = 0,7V
- V Bateria = 8.45V (valor máximo)

4=0,321⋅V BAT−0,7 4=

| | R19 R18R19 | ⋅8,45−0,7

Le daremos un valor a R19 para despejar R18 ; por ejemplo 4K7ohm.

4=

R19

R18R19

⋅8,45−0,74K7R18 ⋅0,52=4K7 De aquí despejamos R18 = 4k3Ω

El valor de ambas resistencias serán iguales, de 4k3Ω, en el mercado no existe ese valor, pero utilizaremos el más cercano que es de 4K7Ω.

Una vez hecho el circuito, visualizamos en el LCD la conversión digital de la tensión máxima y mínima. En nuestro caso hemos obtenido 0864 para la tensión máxima, y 0665 para la mínima. Vemos que hay una diferencia de 199 entre el máximo y el mínimo.

Ya con estos datos sólo tenemos que hacer una regla de 3 para obtener valores entre 1 y 100:

nivel = [(resultado_A/D – valor_mínimo) · 100] / diferencia
nivel = [(resultado_A/D – 665) · 100] / 199
nivel = (resultado -665) · 0.503

A la hora de programar el PIC introduciremos esta formula para visualizar directamente el porcentaje del nivel de batería.

Componentes utilizados:

– | PIC 16f876A
– | Cristal de 4MHz
– | 2 condensadores de 22 pF (para el cristal)
– | 1 condensador de 1uF (para el divisor de tensión)
– | 1 condensador de 330 nF
– | 1 condensador de 100 nF
– | 2 resistencias de 4k7Ω (para el divisor de tensión; calcular para otros
| casos)
– | 1 resistencia de 1KΩ
– | 1 diodo de seguridad 1N4007
– | 1 LM7805
– | 1 pulsador para el Reset
– | Un visualizador LCD
– | 1 batería Li-Po de 7.2V

Código fuente: (en lenguaje C)

/*
Programa para visualizar el nivel de carga de una batería. 2012-2013. G2E LSB. Andoain.
*/
#include <16f876a.h>

#fuses XT, NOWDT, NOPROTECT

#fuses NOLVP,PUT,NOWDT

#fusesNOWRT

#device ADC=10 | //Conversor ADC de 10 bits de resolución

#use fast_io (A)

#use fast_io (B)

#use delay(clock=4000000)

#include <lcd4bitsPIC16.h> | //Incluye funciones del manejo del LCD

int16 resultado, nivel; | //Variable para el resultado de la conversión AD
main()
{
delay_ms(50);
lcd_init(); | //Inicia la pantalla LCD
setup_adc(adc_clock_div_32); //Ajusta frecuencia de muestreo del ADC

while(1)
{
setup_adc_ports(AN0); | //RA0 entrada analógica
set_adc_channel(0); | //Selección del canal 0 (RA0)
delay_us(10); | //Temporiza 10uS
resultado=read_adc(); | //Inicia la conversión y lee el resultado
nivel=(resultado-665)*0.503;

lcd_enviar(LCD_COMANDO,LCD_HOME); | //Colocar el cursor
printf(lcd_putc,"%03Lu %%",nivel); | //Visualiza el resultado
}
}

Linterna de leds:

En este caso necesitamos saber el valor de la resistencia que irá asociada a los 6 leds conectados en paralelo que hacen de linterna en nuestro robot. Sabemos que cada led consume 3.2V y 20mA, por lo tanto usaremos la siguiente fórmula:

Resistencia LED = ( Voltage de la batería - Voltage LED) / Intensidad LED

Como están en paralelo, la intensidad será 20mA · 6 = 120mA

Resistencia = (5V – 3.2V) / 0.12A = 15Ω

Para calcular la potencia: Watts = I² · R = 0.12A² · 15Ω = 0.216W

La resistencia comercial más cercana a estos valores es 15Ω y 250mW.

Asimismo, también tenemos que calcular la resistencia asociada a la base del transistor para que no se produzca ningún cortocircuito:
Sabemos que el transistor BD139 tiene una hfe media de 150.
Ib=Ice/hfe ; 120mA / 150 = 0.8mA
R base= (5V – 0.7V) / 0.8mA = 5375Ω
La resistencia comercial más cercana a ese valor es de 5420Ω.

Consumos:

En lo que se refiere al consumo del circuito hemos listado el consumo de cada uno de nuestros componentes principales con lo que podremos saber cuanto consumiría el robot con todos los dispositivos en funcionamiento máximo y por ello si la batería sera suficiente para soportar el aporte de corriente que se requiere:

- PIC16F876A = 250mA
- | Sonar medidor de distancia con LDR incorporado | SRF08 = 15mA (3mA
en stanby)
- Modulo Bluetooth JY-MCU BT-BOARD V1.04 = 30mA (10mA en stanby)
- | x2 | Servo de Rotación continua | Parallax(Futaba) = 50-140mA (15mA
en stanby)
- x6 Led iluminación luz blanca = 20mA x 6 = 120mA
- x1 Videocámara = 500mA

Viendo estos valores, nuestra batería de 1000mA/h seria suficiente para nuestro robot. Ademas el microcontrolador PIC no consumiría todo eso, ya que

250mA es la corriente máxima que puede soportar el PIC en su patilla VDD | sin
quemarse según lo que viene reflejado en el | datasheet | del fabricante y para nada
llegaría a consumir mas de 100mA en funcionamiento, puesto que no tiene que alimentar casi nada.

En lo que a los servomotores se refiere, su consumo depende del uso que estén teniendo en cada momento y no lo podemos saber con certeza si no tenemos un amperímetro conectado.

6.4-. PLANOS Y ESQUEMAS

Todos los planos y esquemas se adjuntan en los anexos del presente informe:

Anexo II: Planos en Orcad Capture

– | Esquema de bloques general.
– | Esquema del bloque de alimentación.
– | Esquema del bloque de control.
– | Esquema del bloque de potencia.
– | Esquema del bloque de periféricos.

Anexo III: Planos del circuito en Orcad Layout:

– | Circuito principal:
– | Plano general e instrucciones de montaje.
– | Plano de la cara TOP.
– | Plano de la cara BOTTOM.
– | Circuito de la linterna:
– | Plano de la cara TOP.
– | Plano de la cara BOTTOM.

6.5-. PROGRAMACIÓN DEL PIC

La programación del PIC la hemos realizado íntegramente en lenguaje C. Es el cerebro que controla todo el robot.

Para crear el programa, simularlo y cargarlo al PIC, hemos utilizado el programa MPLAB.

Debido a su extensión, el programa completo se encuentro en el Anexo IV del presente informe.

6.6-. CREACIÓN DEL APPLET DE ANDROID

Para dirigir el robot desde una aplicación Android (teléfono o tablet), era necesario crear una aplicación (applet) específica para tal asunto. Hemos utilizado el “MIT App Inventor”, una aplicación web de GOOGLE que permite crear aplicaciones Android sin poseer elevados conocimientos de programación en Java. Con ella hemos creado la interfaz gráfica y el programa que controla el robot.

A continuación se muestra unas imagenes de la interfaz gráfica, asó como el diagrama general de programación.


6.7-. CÁLCULO DEL COSTE DEL PROTOTIPO

A continuación mostraremos los gastos de producción del prototipo, separados en diferentes aspectos, tales como: costes de diseño, costes de materiales y costes de mano de obra.

Un punto importante a tener en cuenta, es que el prototipo ha sido realizado íntegramente por tres técnicos superiores en electrónica, siguiendo las normas de calidad pertinentes. El precio de mano de obra de cada técnico es de 30 € / hora, independientemente dedicados a tareas de diseño, fabricación, montaje, redacción de informes u otros aspectos de este proyecto.

COSTES DE DISEÑO:

Tarea | Nº de horas | Precio / hora | Importe (€)
Diseño del prototipo | 9 | 30 | 270
Creación de planos electrónicos | 30 | 30 | 900
Programación del PIC | 20 | 30 | 600
Creación del applet de Android | 20 | 30 | 600
Realización de informe técnico | 5 | 30 | 150
| | TOTAL | 2.520,00 €

COSTES DE MATERIALES:

Componente | Cantidad | Referencia | Precio unitario(€) | Precio total(€)
Resistencia 1K | 1 | ERJB2AF102V (http://es.farnell.com/panasonic/erjb2af102v/resistencia-potencia-1206-1-1k/dp/1751076) | 0,27 € | 0,27 €
Resistencia 220Ω | 2 | ERJB2AF221V (http://es.farnell.com/panasonic/erjb2af221v/resistencia-potencia-1206-1-220r/dp/1751064) | 0,27 € | 0,54 €
Resistencia 4K7Ω | 4 | ERJB2AF472V (http://es.farnell.com/panasonic/erjb2af472v/resistencia-potencia-1206-1-4k7/dp/1751084) | 0,22 € | 0,88 €
Resistencia 15Ω | 1 | ERJB2AF150V (http://es.farnell.com/panasonic/erjb2af150v/resistencia-potencia-1206-1-15r/dp/1751039) | 0,22 € | 0,22 €

Resistencia 3K9Ω | 1 | ERJB2AF392V (http://es.farnell.com/panasonic/erjb2af392v/resistencia-potencia-1206-1-3k9/dp/1751083) | 0,195 € | 0,195 €
Transistor NPN | 1 | STMICROELECTR ONICS BC139 | 0,35 € | 0,35 €
Condensador 1μ F | 1 | EKMG101ETC1R0 ME11D (http://es.farnell.com/united-chemi-con/ekmg101etc1r0me11d/capacitor-alum-elec-1uf-100v-20/dp/1499818) | 0,23 € | 0,23 €
Condensador 22pF | 2 | MC0805N220J500A 5.08MM (http://es.farnell.com/multicomp/mc0805n220j500a5-08mm/capacitor-ceramic-22pf-50v-c0g/dp/1694230) | 0,033 € | 0,066 €
Condensador 330nF | 1 | MC0805B334K500A 5.08MM (http://es.farnell.com/multicomp/mc0805b334k500a5-08mm/capacitor-ceramic-0-33uf-50v-x7r/dp/1694137) | 0,07 € | 0,07 €
Condensador 100nF | 1 | MC0805Y104Z500A 5.08MM (http://es.farnell.com/multicomp/mc0805104z500a5-08mm/capacitor-ceramic-0-1uf-50v5v-80/dp/1694338) | 0,04 € | 0,04 €
Cristal | 1 | FOXLF040 (http://es.farnell.com/fox-electronics/foxlf040/cristal-4mhz-20-pf-agujero-pasante/dp/2057944) | 0,48 € | 0,48 €
Regulador | 1 | FAIRCHILD SEMICONDUCTOR LM7805CT | 0,69 € | 0,69 €
2 Motores rotación continua Parallax + chasis para robot Home Boe Bot | 1 | Materiales para el "Home Boe Bot" | 75 € | 75 €
Tank Tread Kit (kit para la oruga) | 1 | 28106 | 35 € | 35 €
Interruptor | 1 | SSA12G (http://es.farnell.com/te-connectivity-alcoswitch/ssa12g/switch-slide-spdt-20v-through-hole/dp/6410017) | 3,54 € | 3,54 €
Diodo | 2 | 1N4007 | 0,119 € | 0,238 €
LED, 5mm, Blanco | 6 | OVLEW1CB9 | 1,23 € | 7,38 €
Pulsador | 1 | OMTEN WS050S | 0,38 € | 0,38 €
Bluetooth | 1 | JY-MCU BT BOARD v1.04 | 9,49 € | 9,49 €
Microcontrolador PIC | 1 | PIC16F876A-I/SP (http://es.farnell.com/microchip/pic16f876a-i-sp/ci-mcu-flash-8-bits-16f876-sdil28/dp/9761314) | 4,27 € | 4,27 €
Final de carrera | 2 | HONEYWELL S&C V15W11-DZ200A02-W2 (http://es.farnell.com/honeywell-s-c/v15w11-dz200a02-w2/interruptor-spdt-5a-palanca-recta/dp/2065396) | 7,34 € | 14,68 €
Sonar ultrasónico | 1 | SRF08 | 33,50 € | 33,50 €
Batería LiPo 7.2V | 1 | APB2LP603448 | 20 € | 20 €
Cargador de baterías LiPo | 1 | FU-CLI1000 | 19 € | 19 €
Led encendido verde | 1 | LUMEX SSL-LX5093GT (http://es.farnell.com/lumex/ssl-lx5093gt/led-5mm-green-50mcd-565nm/dp/7605705) | 0,144 € | 0,144 €
Receptáculo, 2,54 mm, simple, 4 vías | 1 | CES-104-01-T-S (http://es.farnell.com/samtec/ces-104-01-t-s/receptaculo-2-54-mm-simple-4-vias/dp/1667510) | 0,54 € | 0,54 €
Conector hembra 12V SMD 2.1mm | 1 | FC68148S (http://es.farnell.com/cliff-electronic-components/fc68148s/dc-socket-smd-dc-10as-2-1mm-pin/dp/1889309) | 1,16 € | 1,16 €

Regleta de conexión con tornillo | 2 | MC24356 (http://es.farnell.com/multicomp/mc24356/terminal-block-eurostyle-2pos-26/dp/1624287) | 0,22 € | 0,44 €
PIC 28 pines | 1 | 2227MC-28-03-05-F1 | 0,99 € | 0,99 €
Caja conector, 1fila, 4 vías | 1 | 65039-033LF | 1,19 € | 1,19 €
Caja conector, 1fila, 5 vías | 1 | 65039-032LF | 1,19 € | 1,19 €
Caja conector, 1fila, 3 vías | 4 | 65039-034LF | 0,90 € | 3,60 €
Caja conector, 1fila, 2 vías | 4 | 65039-035LF | 0,59 € | 2,36 €
Hembra crimpar, 22-26AWG | 1 paquete (100 min) | 47750-000LF | 0,33 € | 33 €
Conector macho, 2,54mm, 1 fila | Tira de 20 | D01-9922046 | 3,35 € | 3,35 €
Hilo de soldar | 2m | 5029075-M 2METRE | 1,50 € | 1,50 €
Placa fotosensible positiva | 1 | KELAN 141300 | 6,74 € | 6,74 €
Cable 26AWG negro | Rollo 25m | NTE ELECTRONICS WH26-00-25 | 3,52 € | 3,52 €
Cámara de video inhalámbrica | 1 | Wireless camera kit | 27,90 € | 27,90 €
| | | TOTAL | 314,13 €

COSTES DE MANO DE OBRA DE FABRICACIÓN:

Tarea | Nº de horas | Precio / hora | Importe (€)
Creación del circuito impreso | 2,5 | 30 | 75
Montaje de componentes electrónicos | 3 | 30 | 90
Montaje del robot | 2 | 30 | 60
Mantenimiento y puesta a punto | 20 | 30 | 600
| | TOTAL | 825,00 €

,COSTES TOTALES:

Descripción | Precio total
Costes de diseño | 2.520,00 €
Costes de materiales | 314,13 €
Costes de mano de obra | 825,00 €
TOTAL | 3.659,13 €

El coste total de este prototipo es de tres mil seiscientos cincuenta y nueve con trece euros (3.659,13 €).
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

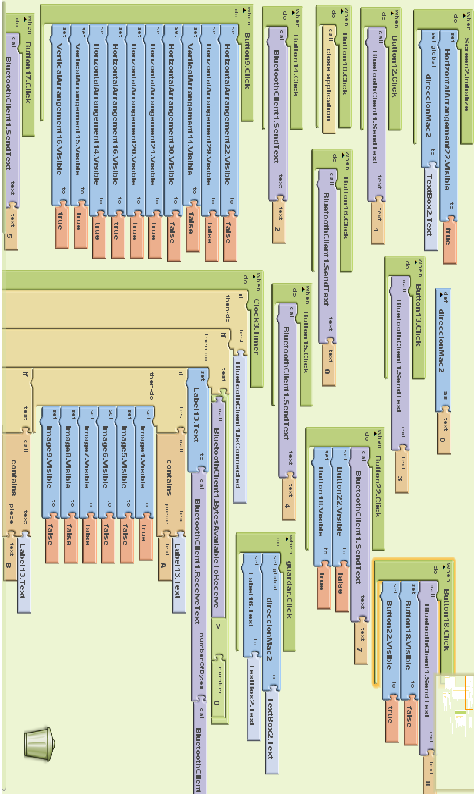
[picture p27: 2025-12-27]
docs/androidmitapp.png

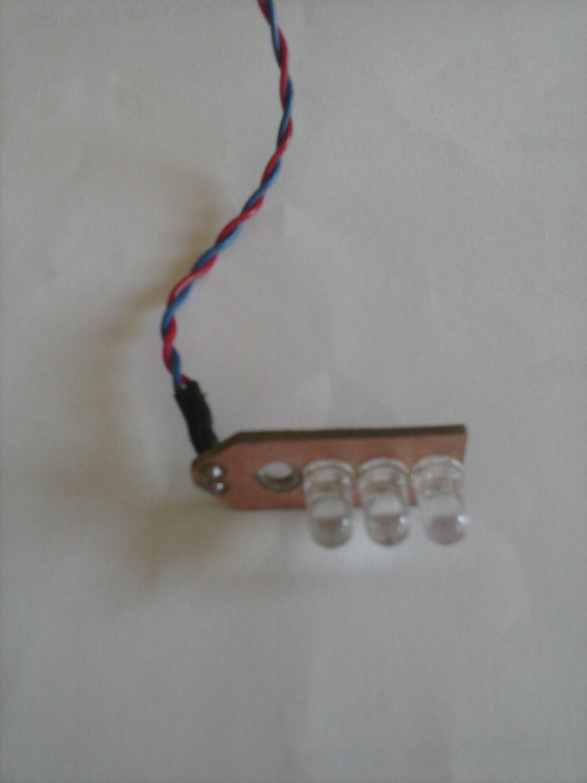
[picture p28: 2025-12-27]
docs/CAM00223.jpg

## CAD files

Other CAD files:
hardware/planos_sketchup/carcasa fina colorl.skp
hardware/planos_sketchup/carcasa final.skp
hardware/planos_sketchup/carcasa_frontal final color.skp
hardware/planos_sketchup/carcasa_frontal final.skp

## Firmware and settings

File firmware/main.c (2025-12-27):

//**************************************************************************************************
//ROBOT EXPLORADOR CURIOSO (ROBOTIC SOLUTIONS S.L.)
//AUTORES: AXIER ALBÍN, JOKIN MUGIKA, AIMAR ROLLÁN
//LSB ANDOAIN. G2E 2012 - 2013
//**************************************************************************************************

#include <16f876A.h>                          
#fuses 	XT, NOLVP, PUT, NOWDT							//Palabra 1 de configuración
#fuses	NOWRT, NOPROTECT 								//Palabra 2 de configuración
#device ADC=10											//Canal analógico de 10 bits
#use fast_io(A)                                         // configuración rápida de entradas y salidas
#use fast_io(B) 
#use fast_io(C) 
#use delay(clock=4000000)								//Frecuencia de trabajo
#use i2c(Master,sda=PIN_C4,scl=PIN_C3,slow,force_hw)	//Configuración blutooth 
#use rs232(baud=9600, xmit=PIN_C6, rcv=PIN_C7)			//Habilita las funciones RS232, velocidad a 9600 baudios
int a,b,c,d,e;											//Definición de variables
int16 distancia,dato,resultado,nivel;					
char distancia_L,distancia_H;                       //buffer de recepción de un dispositivo I2C

#int_ext												//Vector de interrupción externa RB0
	void ext_isr()
	{
		printf("G\r");									//Choque frontal
		a=2;
		b=1;
	}

#int_rda												//Vector de interrupción al recibir por el UART
	tratamiento()
	{	
		switch(getc())									//Lee el carácter recibido
		{
			case '0': a=0; b=0;break;					//Si es el comando es '0', Marcha adelante
			case '1': a=1;break;						//Si es el comando es '1', Marcha atras
			case '2': a=2;break;						//Si es el comando es '2', Parado
			case '3': a=3;break;						//Si es el comando es '3', Curva izquierda
			case '4': a=4;break;						//Si es el comando es '4', Curva derecha 
			case '5': a=5;break;						//Si es el comando es '5', Giro 180º
			case '6': a=6;break;						//Si es el comando es '6', 
			case '7': output_high(PIN_C0);break;        //Encender-Apagar linterna si el comando es '7'
			case '8': output_low(PIN_C0);break;         //Encender-Apagar linterna si el comando es '7'
			
	
		}	
	}

void peligro(void)										//Subrutina que alerta de obstáculos situados a menos de 20 cm
{
	if(distancia < 20 )
	{ 
		printf(" H%c%lucm\r",e,distancia);
	}
	else
	{
		printf(" %c%lucm\r",e,distancia);
	}
}

main()													//Programa principal
{   
	SETUP_ADC_PORTS(RA0_ANALOG);						//Puerta A y B Digitales
	setup_adc(ADC_CLOCK_INTERNAL);
	output_b(0x00);
	set_tris_a(0b00000001);								//Configuración de entradas y salidas
	set_tris_b(0b00011000);								//
	set_tris_c(0b10011110);								//RC6/TxD salida de datos y RC7/RxD entrada del EUSART
	putc('\r');											//Transmite CR
	putc('\n');											//Transmite avance de línea
	enable_interrupts(INT_RDA);							//Activa interrupciónes en la recepción
	enable_interrupts(INT_EXT);
	enable_interrupts(global);							//Habilita interrupciones
	a=2;
	b=0;

	while(1)
	{

		while(a==1&&b==0)								//MARCHA ADELANTE
		{	
			i2c_start(); 								//Arrancamos el sonar
			i2c_write(0xe0);							//Dirección de escritura del sonar
			i2c_write(0x00);							//Ubicacción del registro de comando
			i2c_write(0x51);							//Comando de distancia en cm
			i2c_stop();
			delay_ms(1);  					   			//Entre este delay y el de antes de I2c_start debe de haber 100 ms
			set_adc_channel(0);							//Selección del canal 0 (RA0)
			delay_us(10);								//Temporiza 10uS
			resultado=read_adc();						//Inicia la conversión y lee el resultado
			nivel=(resultado-594)*0.503;

			if(nivel>80)
			{
				e="A";									//Batería 5 barras
			}
			else if(nivel>60 && nivel<80)
			{
				e="B";									//Batería 4 barras
			}
			else if(nivel>40 && nivel<60)
			{
				e="C";									//Batería 3 barras
			}
			else if(nivel>20 && nivel<40)
			{
				e="D"; 									//Batería 2 barras
			}
			else if(nivel>10 && nivel<20)
			{
				e="E"; 									//Batería 1 barras
			}
			else if(nivel>=0 && nivel<10)
			{
				e="F"; 									//Batería 0 barras y color rojo
			}

			delay_ms(1);

			for(d=0;d<4;d++)
			{
				output_high(PIN_A2);
				output_high(PIN_A1);
				delay_us(1300);		
				output_low(PIN_A2);
				delay_us(400);	
				output_low(PIN_A1);
				delay_us(20000);
 			}

	   		output_high(PIN_A2);
			output_high(PIN_A1);
			delay_us(1300);		
			output_low(PIN_A2);
			delay_us(400);	
			output_low(PIN_A1);  
			delay_us(8500); 							//Entre este delay y la siguiente orde que active el motor debe haber 20 mS
 
			i2c_start();
			i2c_write(0xe0);							// dirección de escritura del sonar
			i2c_write(0x01);							// configuración para la lectura de luz y distancia
			i2c_stop();
			i2c_start();
			i2c_write(0xe1);							// dirección del sonar en lectura
			distancia_H=i2c_read(1);					// lee el byt alto de distancia
			distancia_L=i2c_read(0);					// lee el byt alto de distancia
			i2c_stop();
			distancia=make16(distancia_H,distancia_L);	// Valor real de distancia
			peligro();
			delay_us(8500);
		}

		while(a==0) 									//MARCHA ATRÁS
		{	
	
			i2c_start(); 								// arrancamos el sonar
			i2c_write(0xe0);							// dirección de escritura del sonar
			i2c_write(0x00);							// Ubicacción del registro de comando
			i2c_write(0x51);							//Comando de distancia en cm
			i2c_stop();
			delay_ms(1);
			set_adc_channel(0);							//Selección del canal 0 (RA0)
			delay_us(10);								//Temporiza 10uS
			resultado=read_adc();						//Inicia la conversión y lee el resultado
			nivel=(resultado-594)*0.503;
			delay_ms(1);

			for(d=0;d<4;d++)
			{
				output_high(PIN_A1);
				output_high(PIN_A2);
				delay_us(1300);		
				output_low(PIN_A1);
				delay_us(400);	
				output_low(PIN_A2);
				delay_us(20000);  
			}

			output_high(PIN_A1);
			output_high(PIN_A2);
			delay_us(1300);		
			output_low(PIN_A1);
			delay_us(400);	
			output_low(PIN_A2);  
			delay_us(8500);  
			i2c_start();
			i2c_write(0xe0);							// dirección de escritura del sonar
			i2c_write(0x01);							// configuración para la lectura de luz y distancia
			i2c_stop();
			i2c_start();
			i2c_write(0xe1);							// dirección del sonar en lectura
			distancia_H=i2c_read(1);					// lee el byt alto de distancia
			distancia_L=i2c_read(0);					// lee el byt alto de distancia
			i2c_stop();
			distancia=make16(distancia_H,distancia_L);	// Valor real de distancia
			peligro();
			delay_us(8500);
		}

		while(a==2) 									//PARADA
		{	

			i2c_start(); 								// arrancamos el sonar
			i2c_write(0xe0);							// dirección de escritura del sonar
			i2c_write(0x00);							// Ubicacción del registro de comando
			i2c_write(0x51);							//Comando de distancia en cm
			i2c_stop();
			delay_ms(1);
			set_adc_channel(0);							//Selección del canal 0 (RA0)
			delay_us(10);								//Temporiza 10uS
			resultado=read_adc();						//Inicia la conversión y lee el resultado
			nivel=(resultado-594)*0.503;
			if(nivel>80)
			{
				e="A";									//Batería 5 barras
			}
			else if(nivel>60 && nivel<80)
			{
				e="B";									//Batería 4 barras
			}
			else if(nivel>40 && nivel<60)
			{
				e="C";									//Batería 3 barras
			}
			else if(nivel>20 && nivel<40)
			{
				e="D"; 									//Batería 2 barras
			}
			else if(nivel>10 && nivel<20)
			{
				e="E"; 									//Batería 1 barras
			}
			else if(nivel>=0 && nivel<10)
			{
				e="F"; 									//Batería 0 barras y color rojo
			}
			delay_ms(1);
			for(d=0;d<4;d++)
			{
				output_high(PIN_A2);
				output_high(PIN_A1);
				delay_us(1500);
				output_low(PIN_A2);		
				output_low(PIN_A1);
				delay_us(20000);
			}
       		output_high(PIN_A2);
			output_high(PIN_A1);
			delay_us(1500);		
			output_low(PIN_A2);
			output_low(PIN_A1);  
			delay_us(9500);  
			i2c_start();
			i2c_write(0xe0);							// dirección de escritura del sonar
			i2c_write(0x01);							// configuración para la lectura de luz y distancia
			i2c_stop();
			i2c_start();
			i2c_write(0xe1);							// dirección del sonar en lectura
			distancia_H=i2c_read(1);					// lee el byt alto de distancia
			distancia_L=i2c_read(0);					// lee el byt alto de distancia
			i2c_stop();
			distancia=make16(distancia_H,distancia_L);	// Valor real de distancia
			peligro();
			delay_us(7500);
		}

		while(a==3&&b==0) 								//CURVA IZQUIERDA
		{
			i2c_start(); 								//Arrancamos el sonar
			i2c_write(0xe0);							//Dirección de escritura del sonar
			i2c_write(0x00);							//Ubicacción del registro de comando
			i2c_write(0x51);							//Comando de distancia en cm
			i2c_stop();
			delay_ms(1);  					   			//Entre este delay y el de antes de I2c_start debe de haber 100 ms
			set_adc_channel(0);							//Selección del canal 0 (RA0)
			delay_us(10);								//Temporiza 10uS
			resultado=read_adc();						//Inicia la conversión y lee el resultado
			nivel=(resultado-594)*0.503;
					if(nivel>80)
			{
				e="A";									//Batería 5 barras
			}
			else if(nivel>60 && nivel<80)
			{
				e="B";									//Batería 4 barras
			}
			else if(nivel>40 && nivel<60)
			{
				e="C";									//Batería 3 barras
			}
			else if(nivel>20 && nivel<40)
			{
				e="D"; 									//Batería 2 barras
			}
			else if(nivel>10 && nivel<20)
			{
				e="E"; 									//Batería 1 barras
			}
			else if(nivel>=0 && nivel<10)
			{
				e="F"; 									//Batería 0 barras y color rojo
			}
			delay_ms(1);
			for(d=0;d<4;d++)
			{
				output_high(PIN_A2);
				delay_us(1300);
				output_low(PIN_A2);		
				delay_us(20000);
   			}
	   		output_high(PIN_A2);
			delay_us(1300);		
			output_low(PIN_A2); 
			delay_us(13500); 							//Entre este delay y la siguiente orde que active el motor debe haber 20 mS
			i2c_start();
			i2c_write(0xe0);							// dirección de escritura del sonar
			i2c_write(0x01);							// configuración para la lectura de luz y distancia
			i2c_stop();
			i2c_start();
			i2c_write(0xe1);							// dirección del sonar en lectura
			distancia_H=i2c_read(1);					// lee el byt alto de distancia
			distancia_L=i2c_read(0);					// lee el byt alto de distancia
			i2c_stop();
			distancia=make16(distancia_H,distancia_L);	// Valor real de distancia
			peligro();
			delay_us(6500);     	
		}

		while(a==4&&b==0) 								//CURVA DERECHA
		{	
			i2c_start(); 								//Arrancamos el sonar
			i2c_write(0xe0);							//Dirección de escritura del sonar
			i2c_write(0x00);							//Ubicacción del registro de comando
			i2c_write(0x51);							//Comando de distancia en cm
			i2c_stop();
			delay_ms(1);  					   			//Entre este delay y el de antes de I2c_start debe de haber 100 ms
			set_adc_channel(0);							//Selección del canal 0 (RA0)
			delay_us(10);								//Temporiza 10uS
			resultado=read_adc();						//Inicia la conversión y lee el resultado
			nivel=(resultado-594)*0.503;
				if(nivel>80)
			{
				e="A";									//Batería 5 barras
			}
			else if(nivel>60 && nivel<80)
			{
				e="B";									//Batería 4 barras
			}
			else if(nivel>40 && nivel<60)
			{
				e="C";									//Batería 3 barras
			}
			else if(nivel>20 && nivel<40)
			{
				e="D"; 									//Batería 2 barras
			}
			else if(nivel>10 && nivel<20)
			{
				e="E"; 									//Batería 1 barras
			}
			else if(nivel>=0 && nivel<10)
			{
				e="F"; 									//Batería 0 barras y color rojo
			}
			delay_ms(1);
			for(d=0;d<4;d++)
			{
				output_high(PIN_A1);
				delay_us(1700);
				output_low(PIN_A1);		
				delay_us(20000);
   			}
	   		output_high(PIN_A1);
			delay_us(1700);		
			output_low(PIN_A1); 
			delay_us(11500); 							//Entre este delay y la siguiente orde que active el motor debe haber 20 mS
			i2c_start();
			i2c_write(0xe0);							// dirección de escritura del sonar
			i2c_write(0x01);							// configuración para la lectura de luz y distancia
			i2c_stop();
			i2c_start();
			i2c_write(0xe1);							// dirección del sonar en lectura
			distancia_H=i2c_read(1);					// lee el byt alto de distancia
			distancia_L=i2c_read(0);					// lee el byt alto de distancia
			i2c_stop();
			distancia=make16(distancia_H,distancia_L);	// Valor real de distancia
			peligro();
			delay_us(8500);  
		}

		while(a==5&&b==0) 								//GIRO 180º
		{	
			for(c=1;c<=122;c++)
			{
				output_high(PIN_A2);
				output_high(PIN_A1);
				delay_us(1700);
				output_low(PIN_A2);		
				output_low(PIN_A1);
				delay_us(20000);
			}

	 		a=2;
		}

	}	
}

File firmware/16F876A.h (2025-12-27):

//////// Standard Header file for the PIC16F876A device ////////////////
#device PIC16F876A
#nolist
//////// Program memory: 8192x14  Data RAM: 367  Stack: 8
//////// I/O: 22   Analog Pins: 5
//////// Data EEPROM: 256
//////// C Scratch area: 77   ID Location: 2000
//////// Fuses: LP,XT,HS,RC,NOWDT,WDT,NOPUT,PUT,PROTECT,DEBUG,NODEBUG
//////// Fuses: NOPROTECT,NOBROWNOUT,BROWNOUT,LVP,NOLVP,CPD,NOCPD,WRT_50%
//////// Fuses: NOWRT,WRT_25%,WRT_5%
//////// 
////////////////////////////////////////////////////////////////// I/O
// Discrete I/O Functions: SET_TRIS_x(), OUTPUT_x(), INPUT_x(),
//                         PORT_x_PULLUPS(), INPUT(),
//                         OUTPUT_LOW(), OUTPUT_HIGH(),
//                         OUTPUT_FLOAT(), OUTPUT_BIT()
// Constants used to identify pins in the above are:

#define PIN_A0  40
#define PIN_A1  41
#define PIN_A2  42
#define PIN_A3  43
#define PIN_A4  44
#define PIN_A5  45

#define PIN_B0  48
#define PIN_B1  49
#define PIN_B2  50
#define PIN_B3  51
#define PIN_B4  52
#define PIN_B5  53
#define PIN_B6  54
#define PIN_B7  55

#define PIN_C0  56
#define PIN_C1  57
#define PIN_C2  58
#define PIN_C3  59
#define PIN_C4  60
#define PIN_C5  61
#define PIN_C6  62
#define PIN_C7  63

////////////////////////////////////////////////////////////////// Useful defines
#define FALSE 0
#define TRUE 1

#define BYTE int8
#define BOOLEAN int1

#define getc getch
#define fgetc getch
#define getchar getch
#define putc putchar
#define fputc putchar
#define fgets gets
#define fputs puts

////////////////////////////////////////////////////////////////// Control
// Control Functions:  RESET_CPU(), SLEEP(), RESTART_CAUSE()
// Constants returned from RESTART_CAUSE() are:
#define WDT_FROM_SLEEP  3     
#define WDT_TIMEOUT     11    
#define MCLR_FROM_SLEEP 19    
#define MCLR_FROM_RUN   27    
#define NORMAL_POWER_UP 25    
#define BROWNOUT_RESTART 26   

////////////////////////////////////////////////////////////////// Timer 0
// Timer 0 (AKA RTCC)Functions: SETUP_COUNTERS() or SETUP_TIMER_0(),
//                              SET_TIMER0() or SET_RTCC(),
//                              GET_TIMER0() or GET_RTCC()
// Constants used for SETUP_TIMER_0() are:
#define RTCC_INTERNAL   0
#define RTCC_EXT_L_TO_H 32
#define RTCC_EXT_H_TO_L 48

#define RTCC_DIV_1      8
#define RTCC_DIV_2      0
#define RTCC_DIV_4      1
#define RTCC_DIV_8      2
#define RTCC_DIV_16     3
#define RTCC_DIV_32     4
#define RTCC_DIV_64     5
#define RTCC_DIV_128    6
#define RTCC_DIV_256    7


#define RTCC_8_BIT      0     

// Constants used for SETUP_COUNTERS() are the above
// constants for the 1st param and the following for
// the 2nd param:

////////////////////////////////////////////////////////////////// WDT
// Watch Dog Timer Functions: SETUP_WDT() or SETUP_COUNTERS() (see above)
//                            RESTART_WDT()
// WDT base is 18ms
//

#define WDT_18MS        8   
#define WDT_36MS        9   
#define WDT_72MS       10   
#define WDT_144MS      11   
#define WDT_288MS      12   
#define WDT_576MS      13   
#define WDT_1152MS     14   
#define WDT_2304MS     15   

////////////////////////////////////////////////////////////////// Timer 1
// Timer 1 Functions: SETUP_TIMER_1, GET_TIMER1, SET_TIMER1
// Constants used for SETUP_TIMER_1() are:
//      (or (via |) together constants from each group)
#define T1_DISABLED         0
#define T1_INTERNAL         0x85
#define T1_EXTERNAL         0x87
#define T1_EXTERNAL_SYNC    0x83

#define T1_CLK_OUT          8

#define T1_DIV_BY_1         0
#define T1_DIV_BY_2         0x10
#define T1_DIV_BY_4         0x20
#define T1_DIV_BY_8         0x30

////////////////////////////////////////////////////////////////// Timer 2
// Timer 2 Functions: SETUP_TIMER_2, GET_TIMER2, SET_TIMER2
// Constants used for SETUP_TIMER_2() are:
#define T2_DISABLED         0
#define T2_DIV_BY_1         4
#define T2_DIV_BY_4         5
#define T2_DIV_BY_16        6

////////////////////////////////////////////////////////////////// CCP
// CCP Functions: SETUP_CCPx, SET_PWMx_DUTY
// CCP Variables: CCP_x, CCP_x_LOW, CCP_x_HIGH
// Constants used for SETUP_CCPx() are:
#define CCP_OFF                         0
#define CCP_CAPTURE_FE                  4
#define CCP_CAPTURE_RE                  5
#define CCP_CAPTURE_DIV_4               6
#define CCP_CAPTURE_DIV_16              7
#define CCP_COMPARE_SET_ON_MATCH        8
#define CCP_COMPARE_CLR_ON_MATCH        9
#define CCP_COMPARE_INT                 0xA
#define CCP_COMPARE_RESET_TIMER         0xB
#define CCP_PWM                         0xC
#define CCP_PWM_PLUS_1                  0x1c
#define CCP_PWM_PLUS_2                  0x2c
#define CCP_PWM_PLUS_3                  0x3c
#word   CCP_1    =                      getenv("SFR:CCPR1L")
#byte   CCP_1_LOW=                      getenv("SFR:CCPR1L")
#byte   CCP_1_HIGH=                     getenv("SFR:CCPR1H")
#word   CCP_2    =                      getenv("SFR:CCPR2L")
#byte   CCP_2_LOW=                      getenv("SFR:CCPR2L")
#byte   CCP_2_HIGH=                     getenv("SFR:CCPR2H")
////////////////////////////////////////////////////////////////// SPI
// SPI Functions: SETUP_SPI, SPI_WRITE, SPI_READ, SPI_DATA_IN
// Constants used in SETUP_SPI() are:
#define SPI_MASTER       0x20
#define SPI_SLAVE        0x24
#define SPI_L_TO_H       0
#define SPI_H_TO_L       0x10
#define SPI_CLK_DIV_4    0
#define SPI_CLK_DIV_16   1
#define SPI_CLK_DIV_64   2
#define SPI_CLK_T2       3
#define SPI_SS_DISABLED  1

#define SPI_SAMPLE_AT_END 0x8000
#define SPI_XMIT_L_TO_H  0x4000

////////////////////////////////////////////////////////////////// UART
// Constants used in setup_uart() are:
// FALSE - Turn UART off
// TRUE  - Turn UART on
#define UART_ADDRESS           2
#define UART_DATA              4
////////////////////////////////////////////////////////////////// COMP
// Comparator Variables: C1OUT, C2OUT
// Constants used in setup_comparator() are:
#define A0_A3_A1_A3  0xfff04
#define A0_A3_A1_A2_OUT_ON_A4_A5  0xfcf03
#define A0_A3_A1_A3_OUT_ON_A4_A5  0xbcf05
#define NC_NC_NC_NC  0x0ff07
#define A0_A3_A1_A2  0xfff02
#define A0_A3_NC_NC_OUT_ON_A4  0x9ef01
#define A0_VR_A1_VR 0x3ff06
#define A3_VR_A2_VR 0xcff0e
#define CP1_INVERT  0x0000010
#define CP2_INVERT  0x0000020

#bit C1OUT = 0x9c.6      
#bit C2OUT = 0x9c.7      

////////////////////////////////////////////////////////////////// VREF
// Constants used in setup_vref() are:
//
#define VREF_LOW  0xa0
#define VREF_HIGH 0x80
// Or (with |) the above with a number 0-15
#define VREF_A2   0x40
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
